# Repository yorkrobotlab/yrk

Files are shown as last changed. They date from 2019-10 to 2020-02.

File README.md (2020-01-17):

# York Robotics Kit

This is the repository of the York Robotics Kit, designed to allow features rich, ROS-ready robots to be quickly developed using the Raspberry Pi 3 and 4 computer devices.  

The documentation can be view on readthedocs at the following URL:

https://york-robotics-kit.readthedocs.io/en/latest/

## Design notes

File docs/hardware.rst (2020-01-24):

.. include global.rst
.. YRK User Guide: Connecting Hardware

*******************
Connecting Hardware
*******************

This section of the user guide explains how to connect hardware such as batteries, motors, servos and sensors to the **YRK** to make a complete electronics hardware design for a robot.  The simplified
pin-out diagram is shown below, a more detailed view is available in the ``Documents`` sections.

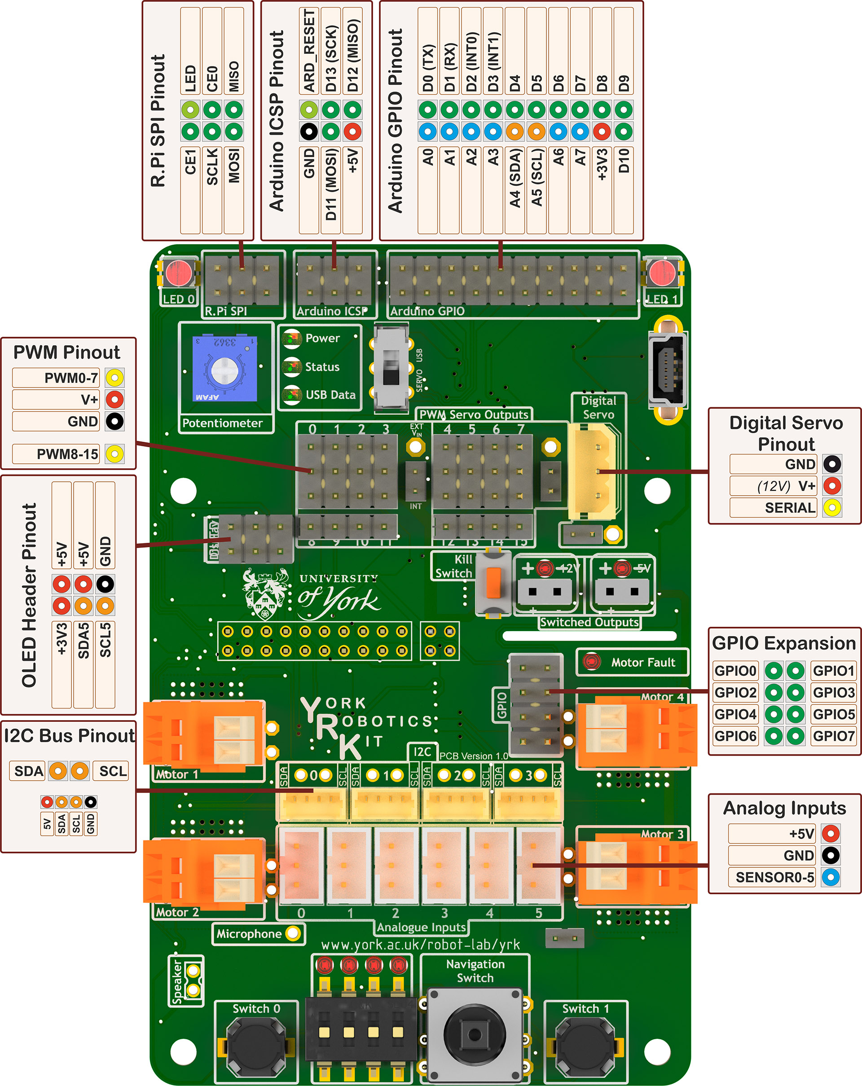
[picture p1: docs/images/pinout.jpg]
Pin-out and wiring diagram for York Robotics Kit


    Pin-out and wiring diagram for York Robotics Kit

Power Supply
------------

The YRK can be powered by any standard 12V power supply with a 2.1mm DC jack (centre positive) and 3A or greater current rating.  Using a tethered power supply such as this is strongly
recommended to be used as much as possible to preserve battery life if motion of the robot is not required.  Do not connect a power supply when the battery is connected and vice-versa *(shutdown
between changing power sources by pressing the power button)*.

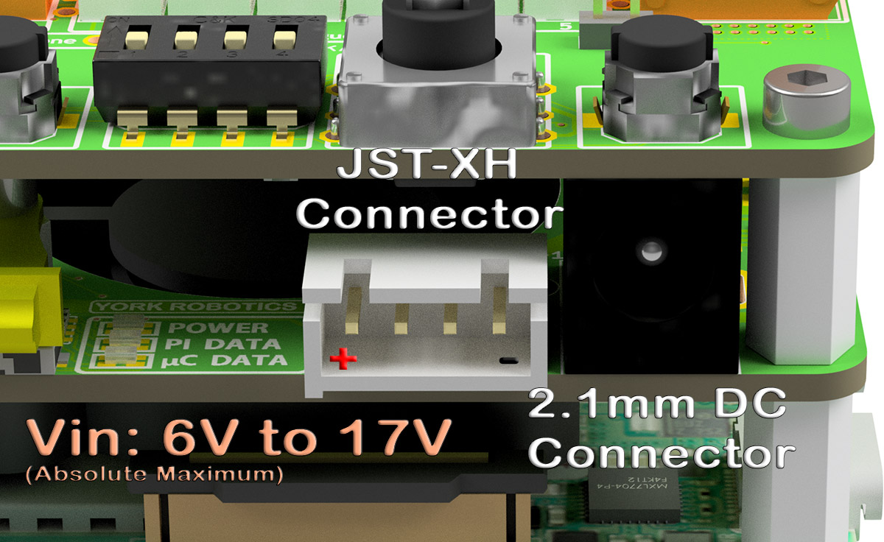
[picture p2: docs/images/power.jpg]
DC power jack and JST-XH power jack at front of YRK on YRL039 power supply board.


    Location of the 2.1mm DC jack and JST-XH battery connector

Battery
-------

The YRK is primarily inteded to be run using a 3-cell Lithium-Polymer battery pack, connected using the industry-standard **JST-XH** 4-pin 0.1" pitch connector
used as the balance charging connector.  These connectors and cables are typically rated for 2A current which is enough for normal use of the YRK [which has a **2.5A** input Polyfuse].  Where high
currents are needed, such as powering multi servo motors, the high current cable from the battery should be soldered *(via a self-made adapter)* to the appropriate power points on the **YRL040** PCB.

The **YRL039** power supply board has a low-voltage dropout and should work effectively from voltages as low as **5.5V** to a **17V** high, enabling 2-cell and 4-cell operation Li-Po (and a range
of other lead-acid, Ni-Mh, NiCad, LiFe and other rechargeable battery technologies, provided they can provide around 5A peak current at 5V).  Relevant changes to the ``yrk.settings`` file should
be made to reflect the battery used if not the default 3-cell configuration.

Only the outer-two connections of the **JST-XH** connector are used.  It is also possible to use the 2.1mm DC jack as the input source.  Always disconnect the battery after use and charge using a
suitable charger (in a fire-safe bag if using a Li-Po battery pack).  The power supply board is not presently optimised for ultra low-current and the residual current draw (from the ATMega microcontroller)
will discharge the battery even when beyond a damagingly low value.  General convention suggest a per-cell voltage of 3.0V is the absolute minimum a Li-Po battery should be allowed to discharge to *(ie 9V
for 11.1V 3-cell battery)* before permanent damage is likely to be done.  The Arduino code on the **YRL039** can be configured to automatically switch off power supplies below a critical low voltage but this
needs to be correctly configured for the battery technology used.  If the ``core.py`` software is *not* run the user must implement some method of periodically monitoring the battery voltage and provide
suitable user warnings when low levels are reached, otherwise batteries can rapidly deteriorate.

The YRK connected to a Raspberry Pi 4 will typically consume approximately 800mA on the 5V rails at idle, most the current powering the Raspberry Pi and a smaller amount of the **5V_AUX** rail (mostly
powering the fan and LEDs).  Motors and sensors will add significantly to this load.  This relatively high idle load means that battery capacity should be at least 1000mAH, and this capacity would
provide at best around 1 hours use *(and significantly less in high load cases)*.  The use of a lower-power Raspberry Pi, such as the model 3A, might be considered when long battery life on small batteries
is desired, at the expense of memory, processing capability and expandability.

DC Motors
---------

There are four serial H-Bridge motor drivers, based on the **DRV8830** `TI Motor Driver <http://www.ti.com/lit/ds/symlink/drv8830.pdf>`_.
The PCB design limits each motor driver to approximately **800mA** current, powered from the *5V_AUX* supply.  Having all four motors drawing this peak current
for sustained periods will exceed the rating of the power supply.  This current limit *(and voltage rating)* does restrict the motor driver to using small motors,
such as the widely-available 3mm shafted **micro-metal gear motors**.  Before using a different size of motor it is recommend to check *(such as by using a bench
PSU)* what the stall and no-load currents at **5V**.

The holes on the unpopulated PCB allow the motors to be connected to either **Wago** push-fit terminals or **(on PCB version 1.1)** 3.5mm pitch screw terminals.
With either connector, a remaining pair of holes will be accessible on the PCB should a direct soldered lead be required.  The motor driver can detect fault
conditions (undervoltage, overvoltage and overtemperature events) and when the ``yrk.core`` program is running these will be indicated by the red fault LED above
the top-right motor output.  If persistent fault conditions check the motor is working correctly and doesn't draw excessive current for the design; micro-metal-gear
motors are relatively delicate.  

Servos
------

The YRK can control both standard analogue servo motors (8 directly attachable, 8 further channels available via breakout), and digital servo motors via an
Arduino-based software interface.

Analogue Servos
^^^^^^^^^^^^^^^

Analogue servos are operated using a **PCA9685** `I2C LED driver IC <https://www.nxp.com/docs/en/data-sheet/PCA9685.pdf>`_.
Whilst primarily designed to allow I2C brightness control of up to 16 LEDs,  it can effectively work as a analogue servo controller.
Analogue servos typically operate with a **20mS** period width *(50Hz PWM frequency)*, and expect a pulse width in the **1ms - 2ms** range [with **1.5ms** being the middle point of the servo rotation].
The **PCA9685** lets us fix the PWM frequency for all outputs and effectively becomes an I2C servo controller.

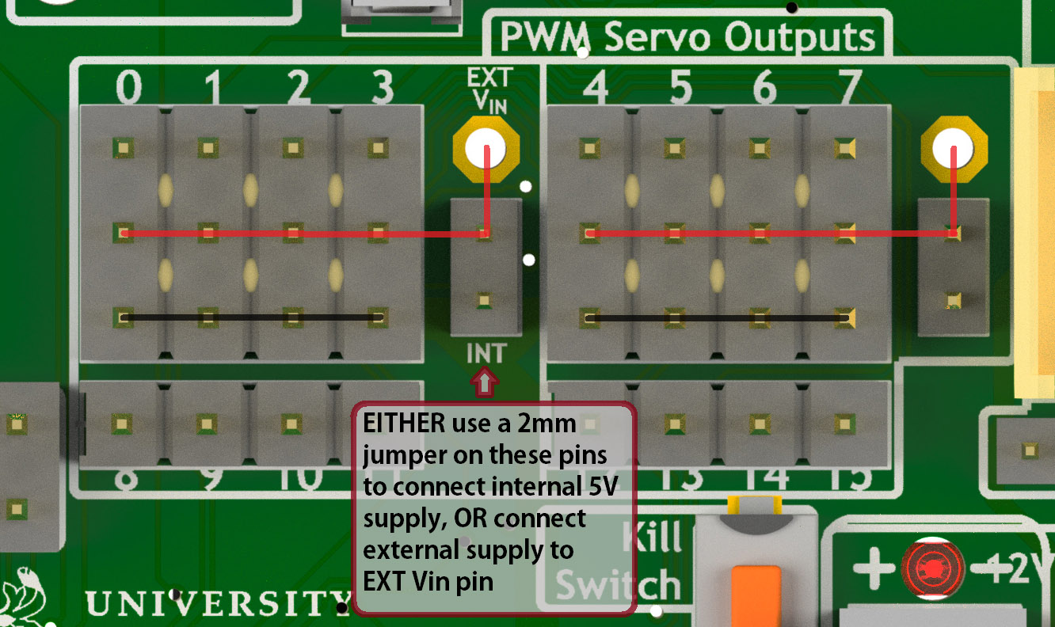
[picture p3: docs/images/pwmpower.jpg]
Power routing for 2 banks of PWM analogue servo outputs


    Power connections for the 2-banks of PWM analogue servo outputs

There are 16 available outputs on the YRL040 PCB, located in the middle-top of the PCB.
Eight of these are available as full 3-pin outputs, where DC power (**+** and **GND**) can be supplied to the servo.
Most analogue servos come hardwired with a three-pin 0.1” pitch socket attached at the wire tail.
Different colour schemes are used for the wiring, and it is important to be careful checking the orientation of the plug;
as a general rule the lightest colour will the control signal (top side of connector) and the darkest will be ground.

==========  =======   ======  ======  ===============
Pin Number  Signal    Futaba  JR      Hitec
==========  =======   ======  ======  ===============
3 [Top]     Control   White   Orange  Yellow or White
2           V+        Red     Red     Red or Brown
1 [Bottom]  Ground    Black   Brown   Black
==========  =======   ======  ======  ===============

These 8 complete connections are split into two banks of four.  Each of these banks can be supplied with DC either by the internal 5V supply **(by using a 2mm jumper)**, or to an external positive input, by soldering a suitable cable onto the hole on the board.  If the internal supply is used, the total current for each bank **must not excede 1A** (a pair of 0603 fuses are included on the board .  This is due to the overall current limitations on the board.  For this reason it is strongly recommended to only use very small, low-current servos, and to spread load across both banks, if using the internal supply.

Another 8 PWM outputs are available just below the primary 8, but these cannot be used directly with a 3-pin connector.  In situations where a large number of servos are required simultaneously, a small break-out board allowing direct power connection would be a sensible option.
The circuit is the same as used on the `Adafruit 16-channel PWM servo driver <https://learn.adafruit.com/16-channel-pwm-servo-driver>`_.

Code for the analogue servo control is in the :mod:`yrk.pwm` module.  Examples of the use of the PWM
driver to control servos can be found in :mod:`examples.console`.

Digital Servos
^^^^^^^^^^^^^^

The York Robotics Kit is designed to support digital servos from the **(Dynamix AX- and MX- series)** via code on the Arduino microcontroller.

To do: This section and code not completed yet!

Analogue Inputs
---------------

The YRK includes an I2C based, 8-channel, 8-bit analogue to digital converter IC.  Whilst this can be used for anything
requiring analogue inputs, it is primarily intended for use with analogue distance
sensors manufactured by Sharp, in particular the **2Y0A21** and **2Y0A41** models.  The reference voltage is set to **2.5V**,
meaning the returned value is approximately equal to the voltage mulitplied by 100.

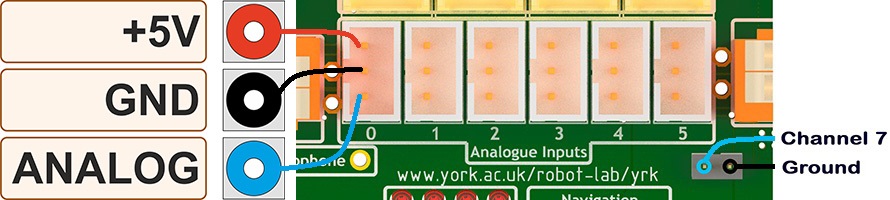
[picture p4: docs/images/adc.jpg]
Pin-out for channels 0-5 and channel 7 of the analog to digital converter


    Analogue input channels 0-5 *(JST PH sockets)* and channel 7

Cables
^^^^^^

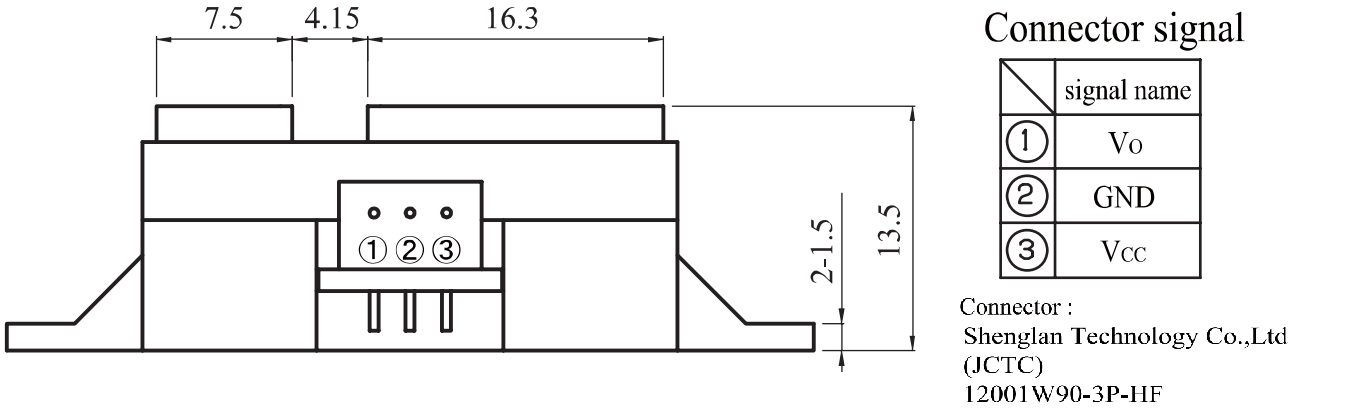
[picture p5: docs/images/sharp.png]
Wiring diagram of Sharp Distance Sensors


    Wiring diagram of Sharp Distance Sensors

The Sharp distance sensors use a 3-pin JST PH series connection **(note the newest models use a JCTC connector instead of
a JST)**.  6 matching JST-PH connections are available on the York Robotics Kit, each providing the analogue-input and 5V
power supply required by the sensor.  A suitable complete pre-made harness has not been sourced, but it is possible to buy
pre-crimped leads from JST which make creating harnesses quick and simple *(if expensive)*.

===============   ============  ===================  ======================
JST Part Number   Farnell Part  Description          Unit Price *[per 100]*
===============   ============  ===================  ======================
01SPHSPH-26L150   2065431       150mm PH-PH Lead     0.416
01SPHSPH-26L300   2065432       300mm PH-PH Lead     0.439
PHR-3             3616198       3-pin PH Receptacle  0.032
===============   ============  ===================  ======================

To assemble the harness, place one receptacle face-up and the other face-down then connect top-to-top, middle-to-middle and bottom-to-bottom,
as seen in the photograph below.

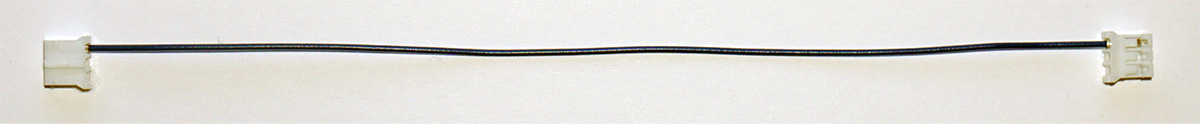
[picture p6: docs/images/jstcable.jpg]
Assembly of a JST PH cable for use with Sharp Distance Sensors


    Assembly of first wire in JST PH cable for use with Sharp Distance Sensors

Datasheets
^^^^^^^^^^

`Sharp 2Y0A21 [10-80cm] <https://global.sharp/products/device/lineup/data/pdf/datasheet/gp2y0a21yk_e.pdf>`_

`Sharp 2Y0A41 [4-40cm] <https://global.sharp/products/device/lineup/data/pdf/datasheet/gp2y0a41sk_e.pdf>`_

Potentiometer
^^^^^^^^^^^^^

Channel 6 of the ADC is connected to a potentiometer *(variable resistor)* at the top-left of the PCB.  As the pot'
is rotated clock-wise from left to right the ADC output value will **decrease** from 255 to 0.

Other ADC Inputs
^^^^^^^^^^^^^^^^

Channel 7 of the ADC is routed to the left pin of a 2mm pitch pin-header below the channel 5 connector.  Any of
channel 0-5 and 7 can be used as a general purpose ADC input (8-bit, with a 2.5V reference voltage) by using the
raw reading value.  There is also the potential to use any of the 8 available analogue inputs on the ATMega microcontroller which offers 10-bit
resolution *(see section on Arduino below)*.

I2C Devices
-----------

The I2C interface is widely used for many robotics sensors and accessories.  The YRK uses a **PCA9548** I2C
switch, which splits the master I2C bus into 8 individual busses, allowing the use of repeated I2C addresses
across multiple ports.  This allows, for example, the use of multiple I2C distance sensors which share the
same I2C address, by connecting them to different busses.  Most I2C devices (capable of operating in **400KHz**
*fast mode*) can be attached provided they do not use the address **0x70** which is used by the switch.

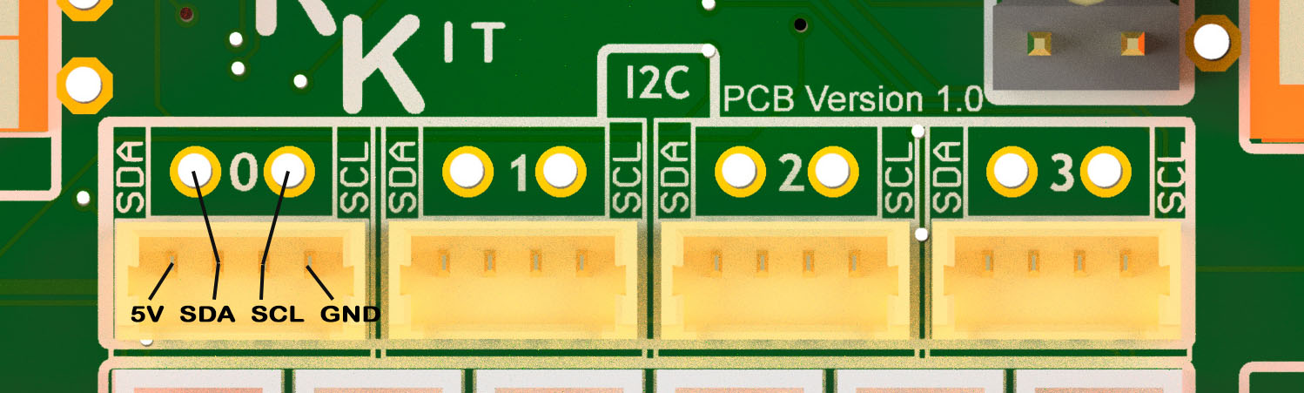
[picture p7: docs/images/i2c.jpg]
Closeup of I2C (channel 0 - 3) Picoblade and 0.1" connectors


    Closeup of I2C (channel 0 - 3) Picoblade and 0.1" connectors

The I2C switch has a kernel-level driver, meaning that the individual switched busses appear to the user as
different I2C root devices (each has its own file handle at ``/dev/`i2c-XX``).  The actual address of the bus
is different when used on the Raspberry Pi 4 hardware and earlier versions, as the Raspberry Pi 4 hardware
can support more native I2C busses (not used in the **YRK**).  On the Raspberry Pi 4, the switched busses map
to file descriptors ``/dev/i2c-6`` to ``/dev/i2c-13`` from channel 0 to 7, and to descriptors ``/dev/i2c-3`` to ``/dev/i2c-10``
on earlier version of the Pi.

The first four channels are unused and are intended for user additions.  These SDA and SCL signals for these channels are each routed to
unpopulated 0.1" pitch holes on the YRK PCB, and also to 4-pin Molex Picoblade headers.  The Picoblade headers (1.25mm pitch) include a
5V and GND signal.  These are directly compatible with sensor boards developed at York such as the **YRL013** multi-sensor board and the
**YRL019** thermal-imaging sensor board.  Note that all i2c channels except channel 4 are pulled-up to 3.3V; channel 4 is
utilised by the PWM driver and the Arduino *(see below)* and is pulled-up to 5V.

Arduino
-------

The YRK includes a **ATMega328P** microcontroller, running at **5V** and connected to both an
FTDI serial to USB interface and to the I2C switch (on switch port 5, which is ``/dev/i2c_11`` on Pi 4).
The microcontroller is effectively a clone of an Arduino Nano board (albeit with a different pin layout).

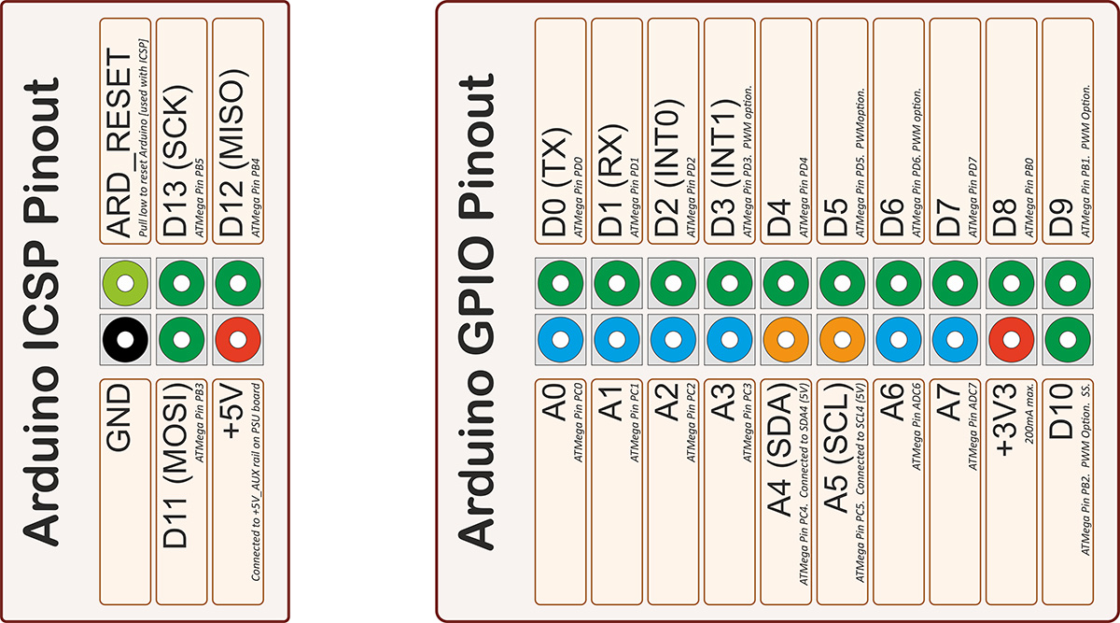
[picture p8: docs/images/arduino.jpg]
Pinout for ATMega microcontroller expansion


    Pin-out for the ATMega microcontroller *(Arduino nano clone)*

Programming Bootloader
^^^^^^^^^^^^^^^^^^^^^^

Before normal use, the ATMega328P must have bootloader code uploaded to it which allows it to be programmed
using the serial to USB interface.  This can be done using various AVR programmers, but can also be done
using a separate Arduino board and the `Arduino as ISP <https://www.arduino.cc/en/tutorial/arduinoISP#toc2>`_
program.  The best settings in the Arduino IDE are to use ``Board: Arduino Pro or Pro Mini`` and ``Processor:  ATMega328P (5V, 16MHz)``.

Uploading Code
^^^^^^^^^^^^^^

Once the bootloader has been uploaded, the Arduino can be programmed via the mini-USB port at the top-left of the board.
Note that the 5V power on the mini-USB is not connected to the YRK *(this means the YRK board needs to be powered on if programming
over USB).  It is possible to program the Arduino from the Raspberry Pi, if a USB cable is connected from the mini-USB to the USBs on the
Pi.  This can be done either using Arduino IDE, or from the command line *(avoiding the need for X-windows)*.  The command line upload
would look similar to this statement::

  arduino --upload --port /dev/ttyUSB0 --board arduino:avr:pro:cpu=16MHzatmega328 --verbose-upload my_code.ino

It is important to note that to use the mini-USB interface the slide-switch must be in its upper position.  The switch
directs the **TX** and **RX** serial output pins from the ATMega microcontroller to either the **FTDI** serial to USB interface *(and mini-USB port)*,
if it is in its upper position, and combines the lines via a tri-state buffer for use with the digital servo port in its lower position.

Switched Outputs
----------------

The board contains a pair of **FET** driven switched outputs which can be used when it is necessary to turn
on simple switched loads.  Typical uses might be powering buzzers and sirens, LED light fittings and lamps,
beacons, solenoids and relays.  One output is connected to the **5V_AUX** supply, the other is marked as **12V** and is
connected to the battery or DC input.  Both switched outputs are protected by a 1A 0603 quick-blow fuse.  The outputs are
connected to 0.1" sockets *(preferred over header as harder to short-circuit)*.

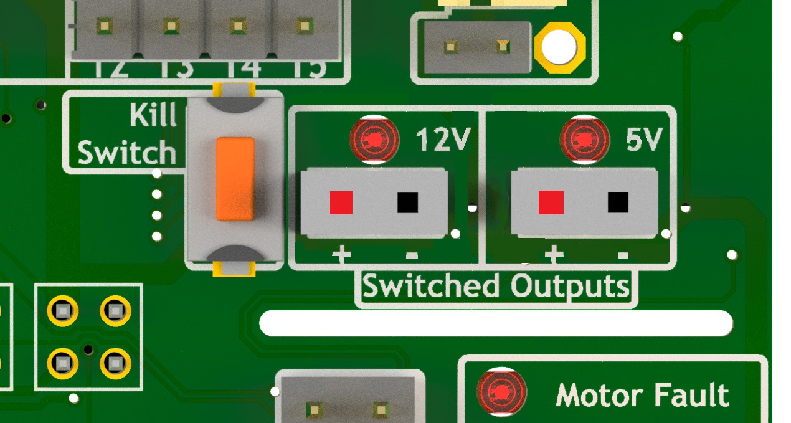
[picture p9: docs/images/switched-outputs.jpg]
Switched output connectors


    Close-up view of 12V and 5V switched output connectors.

It is important to note that the switched outputs use low-side switching, meaning that the **+** output is connected directly
to the *(5V or battery)* supply rail but the **-** is **not** connected to ground; never use the switched outputs on loads
that require the grounds to be coupled together.  It is recommended to limit the current on the switched outputs to below 500mA
if possible.  If a higher current (or circuit with coupled ground) is needed, consider using the switched load to drive a relay
or solid-state equivalent.   Note that the actual potential difference will be a little lower than the indicated amount due to
the voltage drop across the **FET**.  Consider using a flyback diode across inductive loads (such as relays and solenoids).

Raspberry Pi Interfaces
-----------------------

One consequence of the number of hardware features on the board is that very few Raspberry Pi GPIO pins are available for use.  The
5 pins that are available (pins 19, 21, 23, 24 and 26) are the pins that can be used as the SPI0 interface on the Raspberry Pi,
allowing SPI peripherals and expansion to be added to the YRK.  These pins can also be used a general purpose IO pins if the SPI
interface is not required.

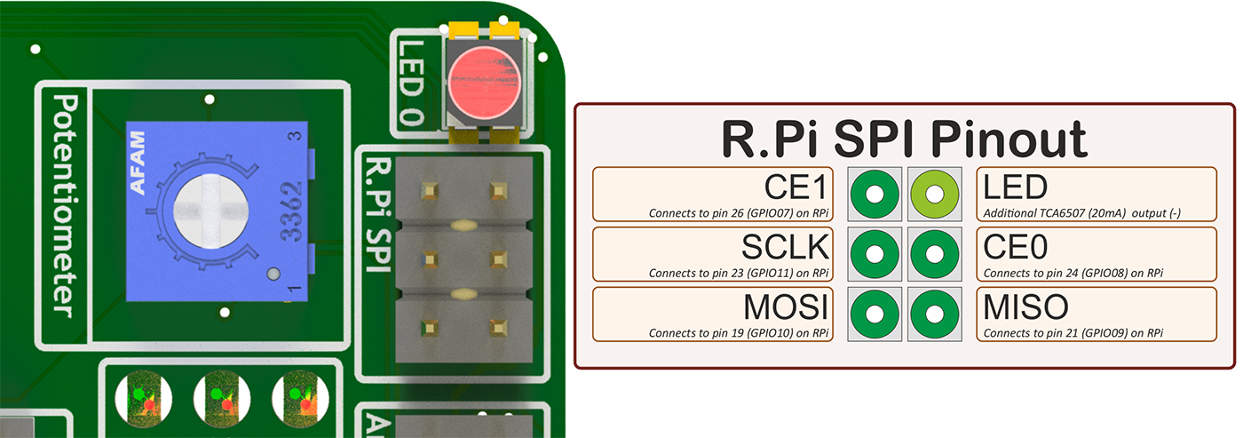
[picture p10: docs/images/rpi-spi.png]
View of RPi - SPi connector


    Close-up view of Raspberry Pi SPI interface at top-left of board (rotated 90 degrees)

Additional GPIO
---------------

A bank of 8 user-GPIO pins connected to the bank 0 of the *(U13)* **PCA9555PW** GPIO expansion IC is available for use.  The API for the pins is
not yet written.

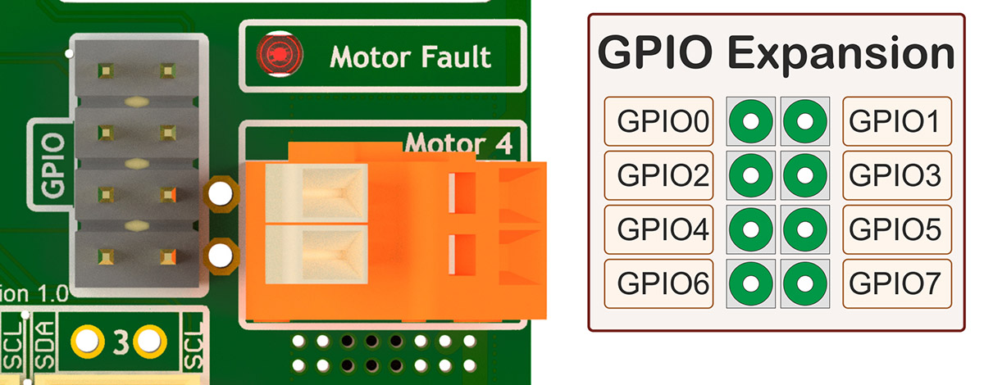
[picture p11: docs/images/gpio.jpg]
View of user GPIO


    Close-up view of 8 user GPIO expansion pins

There are several other expansion pins on the board that can be used as general purpose digital IO pins, for connecting extra hardware
such as switches, LEDs, transistor switches and others.  The **TCA6507** LED driver that drives the RGB LEDs has one additional output that
is configured to give a 20mA drive current to an external LED *(or multiple LEDs in series or parallel)*.  The cathode pin of the LED(s) should
be attached to the LED pin of the ``R.Pi SPI`` header at the top-left of the PCB; the anode can be connected to either a 3.3V or 5V pin as needed
*(blue and white LEDs may require 5V due to their greater forward voltage)*.  The PWM (analogue servo) outputs can also be used to drive LEDs
or other outputs if appropriate *(the PCA9685 driver is actually marketed as a LED driver)*.

Display
-------

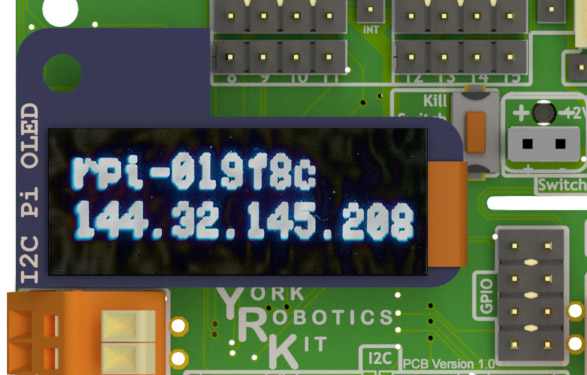
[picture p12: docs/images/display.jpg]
OLED I2C Module attached to the YRK


    Close-up view of Adafruit I2C OLED display module on YRK

The board has been designed such that an **Adafruit PiOLED** 128x32 pixel display module can be directly connected to the main board.
The software library written by Adafruit has been adapted so that it performs more reliably on the switched I2C bus *(note that I2C
is a relatively slow bus and even small displays take quite a lot of data to drive, so infrequent updates are recommended)*.

Obviously it may be desirable to relocate the display elsewhere on a robot chassis if the YRK and Pi are enclosed within; this simply
requires the use of either 4 jumper leads or ideally a **3x2x0.1"** IDC patch cable from the header on the **YRK** to the receptacle on
the display PCB.

It should be possible to use different I2C (and also SPI) displays but some alteration of code may be necessary to handle the i2c switch.
It will not be possible to use any display modules which rely on a large number of GPIO pins on the Raspberry Pi as these are not available
once the YRK is added.  If a larger display is required, consider using the official Raspberry Pi touch display *(7" diagonal)* or a HDMI
based solution.

Loudspeaker
-----------

The YRK includes a monoaural amplifier attached to one of the PWM outputs of the Raspberry Pi **(GPIO12)**.  When correctly configured, the
Raspberry Pi (using the **ALSA** audio system) can be set to play audio using its internal PWM.  The **YRL040** PCB includes a Texas Instruments
`TPA2005 <http://www.ti.com/lit/ds/symlink/tpa2005d1.pdf>`_ class-D audio amplifier IC, which is capable of producing up to 1.4W when using an 8-ohm
speaker.  It may be possible to use lower impedance speakers (down to 4-ohm) but note the amplifier is using the **5V_AUX** and would be operating
out-of-specification at 4-ohms.  Audio generated from PWM outputs is generally very noisy and low in fidelity but is adequate to generate simple
sounds and speech synthesis.

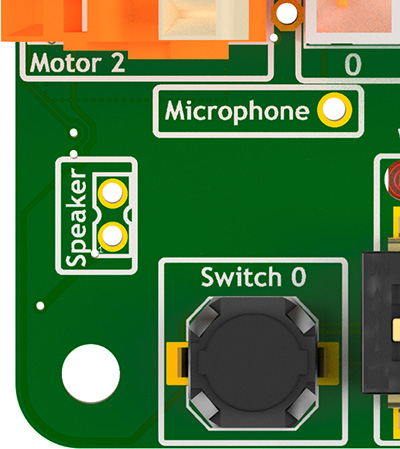
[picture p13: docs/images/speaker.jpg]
Location of speaker connection at bottom left of board


    Location of the speaker connection at bottom left of YRL040 PCB

The speaker output is routed to two pin holes near the bottom-left corner of the **YRL040 PCB** *(being mono the phase of the speaker
doesn't matter)*.  A 2-pin, 2mm pitch header can be soldered in place here to make attaching a removable speaker easier; it hasn't been done by default as
the case has space for a 17mm x 11mm speaker to be connected which would be hard-wired to the underside of the *YRL040* PCB.

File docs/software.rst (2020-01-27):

.. include global.rst
.. YRK User Guide: Software Setup

**************
Software Setup
**************

This user guide covers the software setup of the **YRK**.  It assumes that the micro-SD
card in the Raspberry Pi is using the pre-built **Raspbian** installation (*YRK Raspbian*)
created for the York Robotics Kit, that includes the **ROS Melodic**,  **OpenCV 4** and the
Python 3 virtual environment with all the prerequisite packages installed, along with a clone
of the **Git** repository available at::

   https://github.com/yorkrobotlab/yrk

The detailed software setup procedure followed to create the image is available in a different
document.  In the default image, the username is **pi** and the password is **robotlab**.

YRK Raspbian
------------

This document is written for **YRK Raspbian Build 23/01/2020**.  This build of Raspbian contains
the following software installations:

* Raspbian Version: Buster *(Raspbian GNU/Linux 10)*.  Output of ``lsb_release -a``

* Kernel: Linux 4.19.75-v71+ #1270 Sep 24 2019 armv71.  Output of ``uname -a``

* OpenCV: 4.1.1  Output of ``cv2.__version__`` in Python

* ROS: Melodic  Output of ``rosversion -d``

* Arduino:  1.8.10  Output of ``arduino --version``

The **yrk** PYthon virtual environment is preinstalled with a large number of required packages.
The list of packages can be found in the ``requirements.txt`` file in the ``/home/pi/yrk`` folder,
or by using the ``pip freeze`` command.

First Run
---------

The image is preconfigured to work with the ``robotlab`` wi-fi network at York; if needed, make
changes to ``/etc/network/interfaces`` before booting *(by editing the SD card in a different
Linux system)*, or connect the Pi to a display and configure networking.  Obviously in normal use
the YRK is intended to be connected to remotely using SSH or VNC etc.

On first boot of a clean install of **YRK Raspbian Build 23/01/2020** it is recommended
to update the system.  Make sure all DIP switches are in their **OFF** **(down)** position.
From the ``/home/pi`` folder execute the following script::

  . update.sh

This will update Raspbian using ``apt update`` and ``apt upgrade``,  perform a Raspberry Pi
firmware upgrade using ``rpi-eeprom-update``, run ``fixhostname.sh`` to check the hostname
has been update to the form **rpi-XXXX** *(where XXXX is last 4 digits of MAC address)*.  It
will then update to the latest codebase for **git** using ``git pull``, and clean and rebuild
the HTML documentation using ``make clean`` and ``make html`` from the docs folder.

Once the networking is setup and the system updated, the should be able to use the YRK in its
normal operating mode.  The current release defaults to booting the X-server *(even without display
attached) and auto-login; it is easy and recommended to change to command-line only using the
``raspi-config`` tool if graphical user interface isn't needed.  Both SSH and VNC *(remote-desktop)*
are enabled by default.

The documentation *(this file!)* is built in **HTML** format in the ``/home/pi/yrk/docs/_build/html/``
path, using the **Sphinx** document generation system.

Boot Procedure
--------------

The image contains entries in the ``.bashrc`` file that set the Python virtual environment to
**yrk**.  It then looks to see if the device ``/dev/i2c_11`` exists.  If the **YRK** is connected
and working correctly the i2c multiplexer device tree should be running, enabling 8 extra i2c
busses (named ``/dev/i2c_6`` to ``/dev/i2c_13`` on the **Pi 4** and ``/dev/i2c_3`` to ``/dev/i2c_11`` on the **Pi 3**).

If the device is found, the shell scripts ``/yrk/bootscript.sh`` will be launched.  It is important
to note that both scripts are called every time a new session is started (such as every new **ssh** connection).
A *core program* is run on the first call of ``bootscript.sh`` after each reboot, described in detail in the
next section.  The *core program* writes files to an area of temporary storage at `/mnt/ramdisk/`.  The
**DIP** switches at the bottom of the **YRK** determine the operation mode at boot-up, described in more detail in the next section.

The default working directory is::

   /home/pi/yrk

To kill Python processes, erase the ramdisk and restart ``bootscript.sh`` quickly use the script::

   . rerun

Core Program
------------

The core program :mod:`yrk.core` performs certain core functions that aim to improve usability
and reliability of robot controllers.  This include monitoring battery, temperature and fault
conditions, and monitoring the user switches.  It also provides the functionality to control
the *ROS* service, a web service and a demo program.  This functionality is provided through the
4-way **DIP** switch at the bottom of the kit.

* Switch 0 (*marked as 1 on the switch itself*) determines if the core program should be run on boot.
  If disabled, ``core.py`` will not be run.  This is often useful for testing but user needs to
  remember to keep check on battery and temperature.
* Switch 1 enables the ROS service using ROS launch.  If the switch is disabled after ROS has been
  launched the process will be killed, allowing a relaunch.
* Switch 2 enables the web service.  This enables a **Flask** webserver running a **Dash** site with **DAQ**
  components and this manual.  By default at ``localhost:8080``.
* Switch 3 enables the demo program.  [To do...]

Basic Programming Examples
--------------------------

Before using the ROS infrastructure to program the **YRK** it is worth considering some very simple
low-level example programs.  We shall look at how to write very basic programs that access low-level
features; it is recommended that the core program, normal Python services and ROS services are **not**
running when programming like this.  Remember that if the core program isn't running, automatic battery,
temperature and fault monitoring will not be running.

The code examples in the section are all Python programs that should be run in the **yrk** virtual
environment (this should be enabled by default in the image and is indicated by a ``(yrk)`` before the filepath
in the terminal console).  The examples below can be written in a text-editor, or can be entered directly into
the *Thonny* Python IDE using the VNC connection.  For proper code development working on the Pi over VNC isn't
recommended but it can be useful for quick tests such as this.

Motors Example
^^^^^^^^^^^^^^

The first example program below sets the motor connected to driver 0 *(labelled as Motor 1 on the PCB)* to 50 percent forward
duty-cycle.  We import the :mod:`yrk.motors` module from the **yrk** library as ``motors`` and call the :meth:`yrk.motors.set_motor_speed` method::

  import yrk.motors as motors
  motors.set_motor_speed(0,0.5)

As the **YRK** is designed to be flexible in robot topology, the :mod:`yrk.motors` is limited to functions that affect one motor at a time,
with the exception of :meth:`yrk.motors.stop_all_motors` which sets all 4 outputs to their stopped, high-impedance state.  The following code
shows an example of how simple drive functions for a two-wheels, skid-steered robot, with motors connected to driver 0 and 3 *(labelled as Motor 1
and Motor 4 on the PCB)*.  By adjusting the speeds and the sleep times, it should be possible to make the robot move in a square path::

  import yrk.motors as motors
  import time

  def forwards(speed):
        motors.set_motor_speed(0,speed)
        motors.set_motor_speed(3,speed)

  def turn(speed):
        motors.set_motor_speed(0,speed)
        motors.set_motor_speed(3,-speed)

  def brake_motors():
        motors.brake_motor(0)
        motors.brake_motor(3)

  for i in range(4):
        forwards(0.5)
        time.sleep(0.5)
        brake_motors()
        time.sleep(0.1)
        turn(0.5)
        time.sleep(0.5)
        brake_motors()
        time.sleep(0.1)

   motors.stop_all_motors()

ADC Example
^^^^^^^^^^^

The module :mod:`yrk.adc` contains the methods for reading the analog:digital converter.  The module :mod:`yrk.led` contains
methods for controlling the RGB LEDs.  We can combine all three to use the on-board potentiometer *(attached to ADC channel 6)*
to set the motor speed for driver 0 and set the LED brightness proportional to speed::

  import yrk.adc as adc, yrk.motors as motors, yrk.led as led, time
  while(True):
        #Read raw value of pot. 255 is fully_left, 0 is fully_right
        pot_value = adc.read_adc(6)
        #Set motor 0 speed to be fully backwards [-1.0] at pot=fully_left and
        #fully forwards [1.0] at pot=fully_right
        motors.set_motor_speed(0, 1.0 - (0.007843 * pot_value))
        #Set led brightness to be proportional to speed (range is 0-15)
        led.set_brightness((abs(128-pot_value) + 6) >> 3)
        #Make the LEDs white
        led.set_colour_solid(7)
        #Add a short wait to keep system responsive
        time.sleep(0.01)

.. warning::
   This code will spin motor 0 and set the LEDs to a high brightness unless the potentiometer
   is very close to its central position.

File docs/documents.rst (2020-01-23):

.. include global.rst
.. YRK User Guide: Additional Documents

********************
Additional Documents
********************

This section contains links to other useful documents such as electronic design files, 3D models files
and datasheets for many of the core components use on (or designed for use with) the York Robotics Kit.

.. _schematics:

Schematic Diagrams
------------------

The Eagle design files and bill-of-material files for the **YRL039** and **YRL040** PCB
The schematic diagrams and Eagle design files are available in the ``pcb_documents`` subfolder of the YRK
repository.

========================================================================================   ============================================================================
File                                                                                       Description
========================================================================================   ============================================================================
`yrl039-schematic.pdf </home/pi/yrk/pcb_documents/pdf/yrl039-schematic.pdf>`_              Schematic diagram for the **YRL039** Power Supply Board
`yrl039-top.pdf </home/pi/yrk/pcb_documents/pdf/yrl039-top.pdf>`_                          Top silkscreen view of the **YRL039** Power Supply Board
`yrl039-toptraces.pdf </home/pi/yrk/pcb_documents/pdf/yrl039-toptraces.pdf>`_              Top copper layer view of the **YRL039** Power Supply Board
`yrl039-bottomtraces.pdf </home/pi/yrk/pcb_documents/pdf/yrl039-bottomtraces.pdf>`_        Bottom copper layer view of the **YRL039** Power Supply Board
`yrl040-schematic.pdf </home/pi/yrk/pcb_documents/pdf/yrl040-schematic.pdf>`_              Schematic diagram for the **YRL040** York Robotics Board
`yrl040-top.pdf </home/pi/yrk/pcb_documents/pdf/yrl040-top.pdf>`_                          Top silkscreen view of the **YRL040** York Robotics Board
`yrl040-bottom.pdf </home/pi/yrk/pcb_documents/pdf/yrl040-bottom.pdf>`_                    Bottom silkscreen view of the **YRL040** York Robotics Board
`yrl040-toptraces.pdf </home/pi/yrk/pcb_documents/pdf/yrl040-toptraces.pdf>`_              Top copper layer view of the **YRL040** York Robotics Board
`yrl040-bottomtraces.pdf </home/pi/yrk/pcb_documents/pdf/yrl040-bottomtraces.pdf>`_        Bottom copper layer view of the **YRL040** York Robotics Board
`yrl040-alltraces.pdf </home/pi/yrk/pcb_documents/pdf/yrl040-alltraces.pdf>`_              Bottom view of the **YRL040** York Robotics Board showing both copper layers
========================================================================================   ============================================================================

Datasheets
----------

This table contains internet URLs to most of the core intergrated circuits and modules in use on the **YRL039** and **YRL040** PCBs.

================  ==================  ====================================================================================
Component         Part Name           Datasheet URL
================  ==================  ====================================================================================
Arduino IC        ATMega328P          `<https://www.microchip.com/wwwproducts/en/ATmega328p>`_
I2C Switch IC     PCA9548             `<http://www.ti.com/lit/ds/symlink/pca9548a.pdf>`_
Serial:USB IC     FTDI FT232RL        `<https://www.ftdichip.com/Support/Documents/DataSheets/ICs/DS_FT232R.pdf>`_
Power Supply IC   TPS82130            `<http://www.ti.com/lit/ds/symlink/tps82130.pdf>`_
GPIO Expander IC  PCA9555             `<https://www.nxp.com/docs/en/data-sheet/PCA9555.pdf>`_
LED Driver IC     TCA6507             `<https://www.ti.com/lit/ds/symlink/tca6507.pdf>`_
Motor Driver IC   DRV8830             `<https://www.ti.com/lit/ds/symlink/drv8830.pdf>`_
PWM (Servo) IC    PCA9685             `<https://www.nxp.com/docs/en/data-sheet/PCA9685.pdf>`_
Audio Amp IC      TPA2005             `<http://www.ti.com/lit/ds/symlink/tpa2005d1.pdf>`_
Distance Sensor   GP2Y0A21            `<https://global.sharp/products/device/lineup/data/pdf/datasheet/gp2y0a21yk_e.pdf>`_
Distance Sensor   GP2Y0A41            `<https://global.sharp/products/device/lineup/data/pdf/datasheet/gp2y0a41sk_e.pdf>`_
================  ==================  ====================================================================================

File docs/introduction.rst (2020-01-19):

.. include global.rst
.. YRK User Guide: Introduction

************
Introduction
************

The **York Robotics Kit** is a platform design to allow the Raspberry Pi family of microcomputers
to control a wide variety of robotics hardware with the minimum extra electronics assembly.
It comprises a pair of PCBs which attach above a Raspberry Pi SBC *(single-board computer)*.
This document describes the initial version of the York Robotics Kit, comprising the **YRL039** Power
Supply Board and the YRL040 YRK Board, which are primarily designed to be used with the
Raspberry Pi 4 B and Raspberry Pi 3 B(+) series of computers.

This is still very much a prototype and development design and should be regarded as such!

Construction
------------

.. sidebar:: YRL040 PCB Variants

   **1.0** *[Sep 2019]* Original version as seen in pictures, models and diagrams

   **1.1** *[Dec 2019]* Navigation switch changed to surface-mount model, support for 3.5mm screw terminals for motors added.

This document assumes PCBs have been manufactured and all components assembled **(see separate documentation for PCB construction)**.
The PCBs have been designed using Autodesk Eagle software and are both 2-layer construction, designed to conform to Eurocircuits
Class 6 design guidelines.
Information about the Eagle CAD source files, schematic diagrams and layout documents can be found in the :ref:`schematics` section.
Both PCBs are two-layer boards and designed to be both relatively cheap to manufacture and relatively easy to assemble.

========  ================
PCB Name  Description
========  ================
YRL039    Power Supply PCB
YRL040    Main YRK PCB
========  ================

YRL039 Power Supply
-------------------

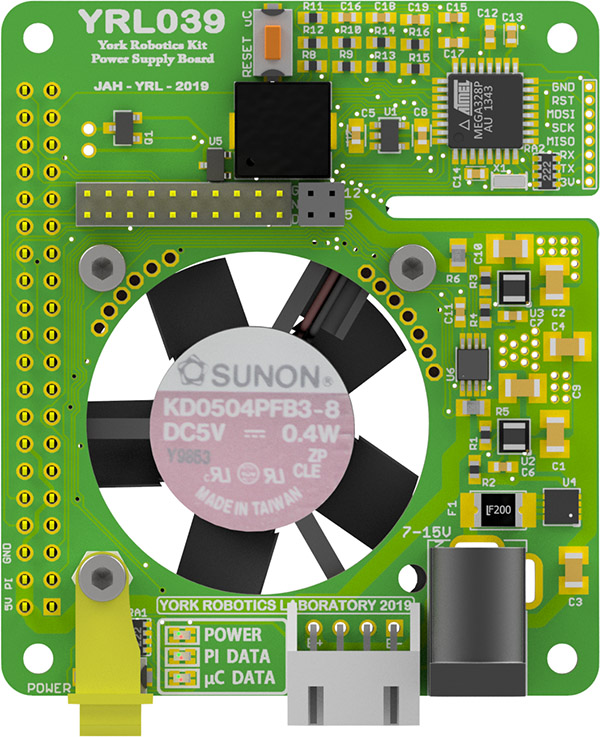
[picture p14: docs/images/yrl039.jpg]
3D rendering of the top of the YRL039 power supply


    YRL039 Power Supply

The YRL039 Power Supply Board as designed to serve six main functions:

* Take a battery or DC input and convert into stable, separate 5V supplies.  Each of the 2 5V supplies is rated to provide at least **2.5A** current.  One supplies the Raspberry Pi *(including USB peripherals)*, the other provides the **5V_AUX** rail for most other components.

* Provide an interface between Pi GPIO pins and respective pins on YRL040 PCB.  It was desired to rotate and reduce in size the 40-pin GPIO header on the Pi to allow more space for edge-mount connectors on either side of the YRL040 PCB **(for motors, sensors and servos etc)**.

* Provide hardware monitoring of temperature, input voltage, output voltages and output currents.

* Provide a software on-off power button with forced shutdown option

* Provide an 35mm fan based active cooling for the Pi microcontroller, the power supplies and the YRL040 mounted above.

* Generate simple audio tones using a Piezo buzzer

All the components except for the fan are mounted to the top-side of the PCB.  The **TPS82130** `TI 3A Step-Down Converter Module <http://www.ti.com/lit/ds/symlink/tps82130.pdf>`_ is core components of each of the two 5V power supplies.

Programming the YRL039
^^^^^^^^^^^^^^^^^^^^^^

The YRL039 uses at ATMega328P microcontroller to control the soft-power switch, make audio tones and report voltage, current and temperature readings using the I2C
bus.  The standard code is found in the ``atmega_code/yrl039_arduino`` subfolder of the GIT repository; if special functionality is required, such as lowering the
battery-low cutoff voltage or reducing the temperature at which the fan operates, it may be necessary to reprogram the microcontroller.  This is easiest to do with
the **YRL030** *FTDI Interface and Programming Board* that contains the 8-pin, 1.25mm pitch connector used for programming and serial data; the **YRL030** can be used
for both flashing the bootloader to the microcontroller using the **ICSP** interface and also uploading code and debugging data using a USB serial interface.

YRL040 Main PCB
---------------

The main YRL040 PCB has been designed such that the vast majority of electronic components are surface mounted on the underside of the board.

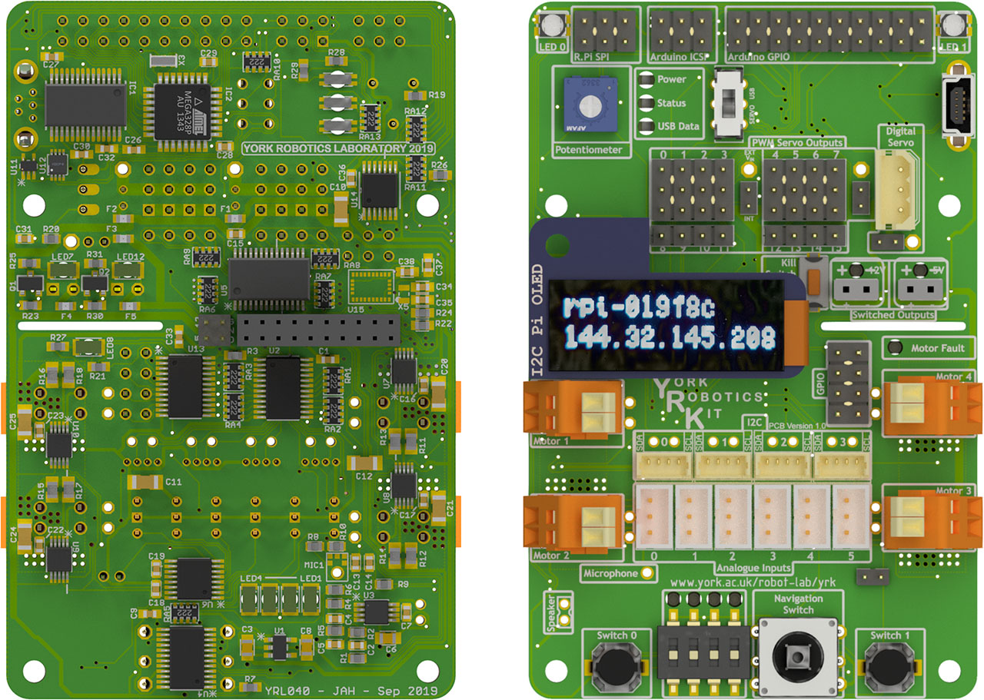
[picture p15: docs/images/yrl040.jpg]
Bottom and top 3D renderings of the top of the YRL040 PCB


    YRL040 Main PCB *(Bottom and Top Views)*

The board contains the following interfaces:

* 8-way I2C switch providing 4 user busses at 3.3V, a 5V bus used by on board PWM driver and Arduino, a bus
  design for use with an OLED display module, a bus for communication with the YRL039 PSU and a bus for all
  other internal connections.

* 4 I2C H-Bridge Motor Drivers based on the TI **DRV8830** IC.

* 16-channel PWM Driver suitable for use with analogue servo motors

* 16-channel GPIO expander providing 5-way navigation switch, 4-way DIP switch, 2 push-button switches and LEDs

* Addition 16-channel GPIO expander providing motor driver fault monitoring, a 5V and a 12V switched output,
  a kill-switch and 8 user GPIO pins

* 8-channel, 8-bit ADC with 6 ports optimised for use with Sharp analogue distance sensors, a channel connected
  to a potentiometer and a spare channel.

* A mono audio amplifier connected to a PWM audio channel on the Raspberry Pi

* An I2S mono microphone module

* An Arduino compatible ATMega328P microcontroller for use with wheel encoding, digital servo motors and other
  tasks.

Assembly
--------

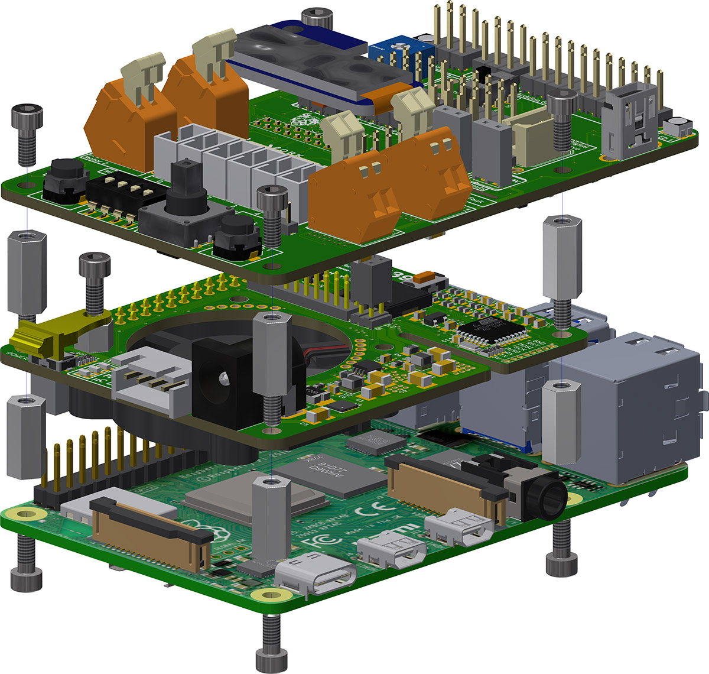
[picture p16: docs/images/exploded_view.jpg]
Exploded view of York Robotics Kit assembly


    Exploded view of YRK showing 11mm standoffs and M2.5 screws

The YRL039 attaches above the Raspberry Pi PCB using the 4 x 11mm length, M2.5 diameter standoffs.  Another layer of 4 x 11mm standoffs is used to attach the *YRL040*
PCB above the **YRL039** power supply PCB.  It is recommended that *M:F* **(male one end, female other)** standoffs are used in the upper layer, with the male threads pointing downwards through the *YRL040* PCB, then M:M standoffs **(sometimes called spacers)** below on the bottom layer.

The assembly can be mounted inside a further case, described below, or can be mounted directly onto a chassis or further standoffs.  Consideration of the airflow path should be taken, particularly when fully enclosed inside a robot.  The Raspberry Pi alone can generate a significant amount of heat and rapidly reaches a point at which it will throttle clock speed if it is not adequately cooled.

Case
----

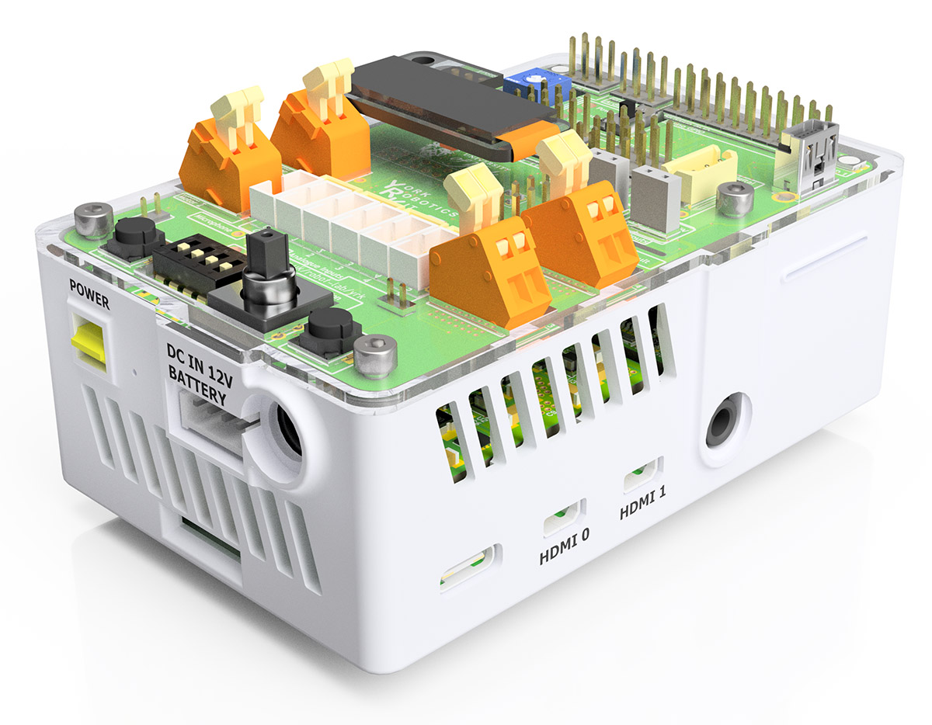
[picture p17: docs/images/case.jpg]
YRK mounted within case


    York Robotics Kit mounted in Polyjet case

A case designed *specifically* for the **Raspberry Pi 4B** series of computer, the **YRL039** and the **YRL040** PCBs has been designed.  This particular design is intended to be printed on a Polyjet class of 3D printer, with very fine tolerancs and gaps.  A more general design for FDM could easily be implemented, but is not essential.  If designed a new housing [or placing assembly within a robot chassis design etc], consider airflow route carefully.  Pi 4 devices will generate substantial heat and the fan needs some route to direct air across the Pi 4 CPU, but also ideally the power supply elements on the top side of YRL039 and also components on the underside of the YRL040 PCB.  Those components likely to dissipate the most heat [motor drivers, PWM driver, amplifier and active outputs] are all towards the lower half of the PCB, which should receive forced convection from the fan.

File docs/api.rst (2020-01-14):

.. include global.rst
.. YRK API modules documentation

************
API Modules
************

The core API python modules are found in the ``yrk`` subfolder.

yrk.adc
-------
.. automodule:: yrk.adc
   :members:

yrk.audio
---------
.. automodule:: yrk.audio
  :members:

yrk.core
--------
.. automodule:: yrk.core
  :members:

yrk.display
-----------
.. automodule:: yrk.display
  :members:

yrk.gpio
--------
.. automodule:: yrk.gpio
  :members:

yrk.led
-------
.. automodule:: yrk.led
  :members:

yrk.motors
----------
.. automodule:: yrk.motors
  :members:

yrk.power
---------
.. automodule:: yrk.power
  :members:

yrk.pwm
-------
  .. automodule:: yrk.pwm
    :members:

yrk.settings
------------
.. automodule:: yrk.settings
  :members:

yrk.switch
----------
.. automodule:: yrk.switch
  :members:

yrk.utils
---------
.. automodule:: yrk.utils
  :members:

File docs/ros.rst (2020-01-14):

.. include global.rst
.. YRK ROS documentation

***********
YRK ROS API
***********

The ROS script, message and service files are found in the catkin workspace subfolder ``catwin_ws/src/yrk_ros``.

This can be quickly accessed from a terminal using the following ROS command::

  roscd yrk_ros

yrk_ros.adc_publisher
---------------------
.. automodule:: catkin_ws.src.yrk_ros.scripts.adc_publisher
  :members:

yrk_ros.button_publisher
------------------------
.. automodule:: catkin_ws.src.yrk_ros.scripts.button_publisher
  :members:

yrk_ros.display_server
----------------------
.. automodule:: catkin_ws.src.yrk_ros.scripts.display_server
  :members:

yrk_ros.led_server
------------------
.. automodule:: catkin_ws.src.yrk_ros.scripts.led_server
  :members:

yrk_ros.motor_server
--------------------
.. automodule:: catkin_ws.src.yrk_ros.scripts.motor_server
  :members:

yrk_ros.power_monitor
---------------------
.. automodule:: catkin_ws.src.yrk_ros.scripts.power_monitor
  :members:

yrk_ros.switched_output_server
------------------------------
.. automodule:: catkin_ws.src.yrk_ros.scripts.switched_output_server
  :members:

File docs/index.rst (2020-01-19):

.. include global.rst

.. YRK documentation master file

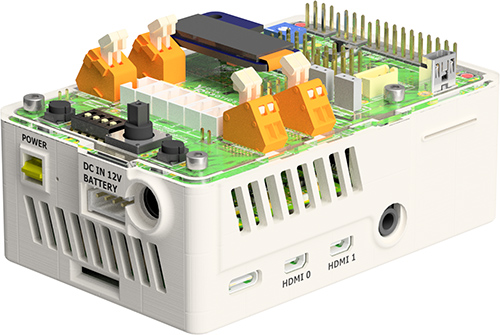
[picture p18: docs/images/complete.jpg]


.. toctree::
   :maxdepth: 2
   :caption: Contents:

   introduction
   hardware
   software
   api
   examples
   ros
   documents

*****
Index
*****

* :ref:`genindex`
* :ref:`modindex`
* :ref:`search`

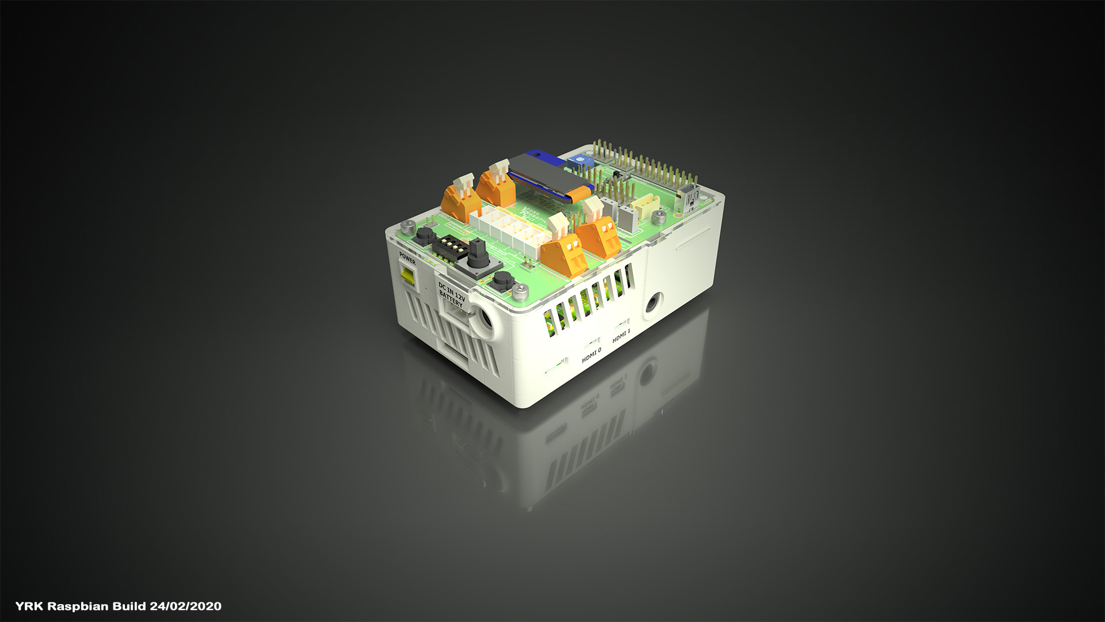
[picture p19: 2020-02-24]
pcb_documents/wallpaper.jpg

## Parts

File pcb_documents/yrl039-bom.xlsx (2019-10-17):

Part | Type | Value | Specs | Package | Manufacturer | Farnell | Other OC | Price
C1 | Capacitor | 10uF 25V | MLCC, min 20V, X7R pref. | C1210 |  | * |  | RS: 0.16each@50 172-1579 Taiyo Yden 1210 10uF 25V X7R Mouser cheaper still. Farnell 50p+
C2 | Capacitor | 10uF 25V | MLCC, min 20V, X7R pref. | C1210 |  | * |  | RS: 0.16each@50 172-1579 Taiyo Yden 1210 10uF 25V X7R Mouser cheaper still. Farnell 50p+
C3 | Capacitor | 10uF 25V | MLCC, min 20V, X7R pref. | C1210 |  | * |  | RS: 0.16each@50 172-1579 Taiyo Yden 1210 10uF 25V X7R Mouser cheaper still. Farnell 50p+
C4 | Capacitor | 10uF 25V | MLCC, min 20V, X7R pref. | C1210 |  | * |  | RS: 0.16each@50 172-1579 Taiyo Yden 1210 10uF 25V X7R Mouser cheaper still. Farnell 50p+
C5 | Capacitor | 1u 25V | MLCC, min 20V, X7R pref. | C0805
C6 | Capacitor | 3.3nF | MLCC | C0603
C7 | Capacitor | 3.3nF | MLCC | C0603
C8 | Capacitor | 1uF | MLCC | C0805
C9 | Capacitor | 47uF 10V | MLCC, min 8V, X7R pref. | C1210
C10 | Capacitor | 47uF 10V | MLCC, min 8V, X7R pref. | C1210
C11 | Capacitor | 100nF | MLCC | C0603 |  |  |  |  | Stock
C12 | Capacitor | 100nF | MLCC | C0603 |  |  |  |  | Stock
C13 | Capacitor | 1uF | MLCC | C0603
C14 | Capacitor | 100nF | MLCC | C0603 |  |  |  |  | Stock
C15 | Capacitor | 100nF | MLCC | C0603 |  |  |  |  | Stock
C16 | Capacitor | 100nF | MLCC | C0603 |  |  |  |  | Stock
C17 | Capacitor | 100nF | MLCC | C0603 |  |  |  |  | Stock
C18 | Capacitor | 100nF | MLCC | C0603 |  |  |  |  | Stock
C19 | Capacitor | 100nF | MLCC | C0603
F1 | Polyfuse | 1812L260/16 | 2.6A HC, 5A TC, 16V | F1812 | Littelfuse | 2786593 |  | 1.2
FAN | Fan | MF35060V2-1000U-A99 | 35x35x6mm 5V | 35x35x6mm | Sunon |  | Mouser: 369-MF35060V21UA99 | 9.75
J2-A | Connector |  |  |  | Samtec
J2-B | Connector | CONNECTOR-PAIRS |  | CONNECTOR-PAIRS | Samtec
J3 | Connector | RAPC722X | 2.1mm DC Socket | Through Hole | Switchcraft | 1608727 |  | 0.779
J4 | Connector | S4B-XH-A | 4-way RA XH Connector | 2.5mm Pitch RA TH | JST | 1516291 | RS: 820-1589 | 0.15 | MOQ 100@Farnell
LED1 | LED | HSMF-C165 | Bi-Colour LED | SMD0.8x1.6 | Broadcom | 8554587 |  | 0.33
LED2 | LED | HSMF-C165 | Bi-Colour LED | SMD0.8x1.6 | Broadcom | 8554587 |  | 0.33
LED3 | LED | HSMF-C165 | Bi-Colour LED | SMD0.8x1.6 | Broadcom | 8554587 |  | 0.33
PCB1 | Connector | RPI3 |  | RPI3
PZ1 | Sounder | PKMCS0909E4000 |  | 9mm Square | Murata | 2529461 |  | 1.1
Q1 | Transistor | FDV303N | N-MOS | FDV303N-SOT-23-NMOS | On Semi | 9845020 |  | 0.248
R1 | Resistor | 523k |  | R0603 | Panasonic | 2303294 |  | 0.0381
R2 | Resistor | 100k |  | R0603 |  |  |  |  | Stock
R3 | Resistor | 523k |  | R0603 | Panasonic | 2303294 |  | 0.0381
R4 | Resistor | 100k |  | R0603 |  |  |  |  | Stock
R5 | Resistor | 5m |  | R0805 |  | 2729138 |  | 0.39 | MOQ 10
R6 | Resistor | 5m |  | R0805 |  | 2729138 |  | 0.39 | MOQ 10
R7 | Resistor | 1K |  | R0603 |  |  |  |  | Stock
R8 | Resistor | 100 |  | R0603 |  |  |  |  | Stock
R9 | Resistor | 400K |  | R0603 |  | 2447366
R10 | Resistor | 100K |  | R0603 |  |  |  |  | Stock
R11 | Resistor | 10K |  | R0603 |  |  |  |  | Stock
R12 | Resistor | 10K |  | R0603 |  |  |  |  | Stock
R13 | Resistor | 400K |  | R0603 |  | 2447366
R14 | Resistor | 100K |  | R0603 |  |  |  |  | Stock
R15 | Resistor | 1M4 |  | R0603
R16 | Resistor | 100K |  | R0603 |  |  |  |  | Stock
RA1 | Resistor Array | CAY16-102J4LF | 1K 4-Element Array | 1206-RES-ARRAY | Bourns | 1770133 |  | 0.06
RA2 | Resistor Array | CAY16-102J4LF | 1K 4-Element Array | 1206-RES-ARRAY | Bourns | 1770133 |  | 0.06
SW1 | Switch | DTSM-32S-B | DTSM-3 Series | 6X3.5-SWITCH | Multicomp | 9471898 |  | 0.17 | MOQ 15 Farnell
SW2 | Switch | DTSM-32S-B | DTSM-3 Series | 6X3.5-SWITCH | Multicomp | 9471898 |  | 0.17 | MOQ 15 Farnell
U1 | Regulator | NCP718BSN330T1G | 2.5V-24V 3.3V Out LDO Reg ["GCH"] | TSOT-23-5 | On Semi |  |  |  | OOS Farnell [2mnth], 12-day RS [185-9270], 1 mnth mouser.
U2 | VR Module | TPS82130 |  | TPS82130-MODULE | Texas Inst. | N/A | RS: 133-0778 | 3.29 | Not yet stocked Farnell [3007470,3008331]
U3 | VR Module | TPS82130 |  | TPS82130-MODULE | Texas Inst. | N/A | RS: 133-0778 | 3.29 | Not yet stocked Farnell [3007470,3008331]
U4 | Protection IC | FR014H5JZ |  | FR014H5JZ | On Semi | 2322491 |  | 0.697
U5 | Temp Sensor | TC1046VNBTR | 6.25mV/C 0C=424mV | SOT-23 | Microchip | 1212685 |  | 0.49
U6 | CS Amplifier | INA2180A2IDGKT | A2 Version gain=50 | SOP65P490X110-9N | Texas Inst. | 2842971 |  | 0.662
U7 | Microcontroller | ATMEGA328P-AU |  | TQFP32-08 | Microchip | 1715486 |  | 1.5
X1 | Resonator | CSTCE8 8MHz Res. |  | RESONATOR | Murata | N/A | RS: 721-4827 283-961 Mouser: 81-CSTCE8M00GH5C99R0

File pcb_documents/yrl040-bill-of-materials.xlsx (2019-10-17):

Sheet: By Component
Part | Quantity | Value | Description | Package | Farnell | Notes
C1,7,9,14-19,22,23,26,27,29-33,36-38 | 21 | 100n | Capacitor 0603 X5R+ 16V+ | C0603
C2 | 1 | 33n | Capacitor 0603 X5R+ 16V+ | C0603
C3,6,8 | 3 | 4.7uF | Capacitor 0805 X5R+ 6.3V+ | C0805
C4,5 | 2 | 10n | Capacitor 0603 X5R+ 16V+ | C0603
C10-12,20,21,24,25 | 7 | 10uF | Capacitor 1206 X5R+ 6.3V+ 10uF+ | C1206
C13 | 1 | 200p | Capacitor 0603 C0G 10V+ | C0603
C28 | 1 | 1u | Capacitor 0603 X5R+ 6.3V+ | C0603
C34,35 | 2 | 22pF | Capacitor 0603 C0G 10V+ | C0603
F1-5 | 5 | 1A | Fuse 0603 1A Fast Acting 20V+ | F0603 | 1337408
IC1 | 1 | FT232RL | USB:Serial Interface | SSOP28 | 1146032
IC2 | 1 | ATMEGA328P-AU | Microcontroller | TQFP32-08 | 1715486
J1 |  | CONNECTOR-PAIRS | CONNECTOR-PAIRS | CONNECTOR-PAIRS
J2-5 | 4 | Picoblade 4-Pin | Picoblade 4-pin TH Header | 4x1.25mm | 9733060
J6 |  | YRL012-EXPORTED_ADA-128X32-DISPLAY | YRL012-EXPORTED_ADA-128X32-DISPLAY | YRL012-EXPORTED_I2C_PI_OLED
J7 |  | SERVO_CONNECTION_BLOCK | SERVO_CONNECTION_BLOCK | SERVO_BLOCK_8X2
J8,9,16,17 | 4 | 233-502 | Wago 2-Way Terminal Block | 2.54mmx2 | 1777096
J10-15 | 6 | SHARP-SENSOR | SHARP-SENSOR | JST-3PIN-PH
J18 | 1 | MINI-USB | MINI-USB | MINIUSB-VERT-1841175 | 1841175
J19 |  | ARDUINO-CONNECTORS | ARDUINO-CONNECTORS | 2X10-PIN-ARDUINO
J21 |  | MOLEX3PIN-9979620 | MOLEX3PIN-9979620 | MOLEX-3PIN-9979620
J22 |  | GPIO-8PIN | GPIO-8PIN | 4X2X0.1-GPIO"
J23,24 | 2 | SPO-2-PIN-HEADER | SPO-2-PIN-HEADER | 2-PIN-SPO
LED1-4 | 4 | KPTL LED | Kingbright Reverse Mount LED, Yellow | LED1206-REV | 2217902
LED5,6 | 2 | RGB LED | Bourns ASMB-MTB0-0A3A2 RGB LED | LED2.4mm | 2401105
LED7,8,12 | 3 | KPTL LED | Kingbright Reverse Mount LED, Red | LED1206-REV | 2217900
LED9-11 | 3 | SML825 LED | ROHM SML-825MVWT86 Bi-Colour Rev. Mount LED | LED1305-REV | 2908899
MIC1 | 1 | SPH0645LM4H-B | MEMS Microphone |  |  | MOUSER: 721-SPH0645LM4H-B
Q1,2 | 2 | BSR802N-MOSFET-2443469 | BSR802N-MOSFET-2443469 | BSR802N-NMOS | 2443469
R1 | 1 | 270 | Resistor 0603 | R0603
R2 | 1 | 150 | Resistor 0603 | R0603
R3 | 1 | 4.7k | Resistor 0603 | R0603
R4-6,19 | 4 | 100K | Resistor 0603 | R0603
R7,20-24,26,30 | 8 | 10K | Resistor 0603 | R0603
R8-10 | 3 | 51 | Resistor 0603 | R0603
R11-18 | 8 | 500m | Current Sense Resistor 0805 250mW+ | R0805 | 1506145
R25,31 | 2 | 1K | Resistor 0603 | R0603
R27 | 1 | 220 | Resistor 0603 | R0603
R28,29 | 2 | 470 | Resistor 0603 | R0603
RA1-4 | 4 | 2k2 | Resistor Array 1206 | RA1206-4 | 1770134
RA5,10,13 | 3 | 1K | Resistor Array 1206 | RA1206-4 | 1770133
RA6-9 | 4 | 220 | Resistor Array 1206 | RA1206-4 | 2321743
RA11,12 | 2 | 100 | Resistor Array 1206 | RA1206-4 | 1770131
SW1 | 1 | 4-Way DIP Switch | SM 4-Way DIP [1825058-7] | 4x0.1" | 2468733
SW2,3 | 2 | Push Button | Panasonic EVPAS Series | 6x6.1mm | 2425608
SW4 | 1 | Nav Switch | ALPS SKQUCAA010 |  |  | OBSOLETE! Replace with SM version in next PCB revision
SW5 | 1 | DPDT Switch | C&K JS202011CQN | 0.1" Pitch TH | 2320018
SW6 | 1 | SWITCH-9471898 | SWITCH-9471898 | 6X3.5-SWITCH
U1 | 1 | MCP1824T-3302E/OT | MCP1824T-3302E/OT | SOT95P270X145-5N
U2 | 1 | PCA9548APWR | PCA9548APWR | SOP65P640X120-24N
U3 | 1 | TPA2005D1DGN | TI Audio Amplifier | MSOP-8 | 2075395
U4,13 | 2 | PCA9555PW,118 | GPIO Expander, NXP or TI | TSSOP-24 | 8906084
U5 | 1 | PCA9685PW | NXP LED {PWM} Driver | TSSOP-28 | 1854074
U6 | 1 | ADS7830IPWTG4 | Octal ADC | TSSOP-16 | 1180129
U7-10 | 4 | DRV8830DGQR | TI Motor Driver | TSSOP-10 | 1863106
U11 | 1 | SN74AHCT1G04DCKT | Inverter, 1 input | SC-70-5 | 1902169 | New order code soon
U12 | 1 | SN74LVC2G126DCUT-1741035 | Buffer | VSSOP-8 |  | No longer stocked @ Farnell. MOUSER: 595-SN74LVC2G126DCUR
U14 | 1 | TCA6507PW | TI LED Driver | TSSOP-14 | 1647813 | Till stock exhausted
U15 | 1 | BNO055 | MICROBUILDER_BNO055 | MICROBUILDER_BNO055 |  | MOUSER: 262-BNO055
VR1 | 1 | 200K Pot | 3386F-1-204TLF | TH | 9354670
X1,2,4 | 3 | CON-MOLEX_87758-0216 | CON-MOLEX_87758-0216 | CON-MOLEX_87758-0216
X3 | 1 | CSTCE16 16MHz Res. | 0011_CSTCE16M0V53-R0 | RESONATOR |  | OBSOLETE, None at Farnell
X5 | 1 | 32.768kHz | SMD Crystall | CRYSTAL-2X1.2 | 2819313

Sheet: By Part Number
Part | Value | Description | Package | Farnell | Notes
C1 | 100n | Capacitor 0603 X5R+ 16V+ | C0603
C2 | 33n | Capacitor 0603 X5R+ 16V+ | C0603
C3 | 4.7uF | Capacitor 0805 X5R+ 6.3V+ | C0805
C4 | 10n | Capacitor 0603 X5R+ 16V+ | C0603
C5 | 10n | Capacitor 0603 X5R+ 16V+ | C0603
C6 | 4.7uF | Capacitor 0805 X5R+ 6.3V+ | C0805
C7 | 100n | Capacitor 0603 X5R+ 16V+ | C0603
C8 | 4.7uF | Capacitor 0805 X5R+ 6.3V+ | C0805
C9 | 100n | Capacitor 0603 X5R+ 16V+ | C0603
C10 | 10uF | Capacitor 1206 X5R+ 6.3V+ 10uF+ | C1206
C11 | 10uF | Capacitor 1206 X5R+ 6.3V+ 10uF+ | C1206
C12 | 10uF | Capacitor 1206 X5R+ 6.3V+ 10uF+ | C1206
C13 | 200p | Capacitor 0603 C0G 10V+ | C0603
C14 | 100n | Capacitor 0603 X5R+ 16V+ | C0603
C15 | 100n | Capacitor 0603 X5R+ 16V+ | C0603
C16 | 100n | Capacitor 0603 X5R+ 16V+ | C0603
C17 | 100n | Capacitor 0603 X5R+ 16V+ | C0603
C18 | 100n | Capacitor 0603 X5R+ 16V+ | C0603
C19 | 100n | Capacitor 0603 X5R+ 16V+ | C0603
C20 | 10uF | Capacitor 1206 X5R+ 6.3V+ 10uF+ | C1206
C21 | 10uF | Capacitor 1206 X5R+ 6.3V+ 10uF+ | C1206
C22 | 100n | Capacitor 0603 X5R+ 16V+ | C0603
C23 | 100n | Capacitor 0603 X5R+ 16V+ | C0603
C24 | 10uF | Capacitor 1206 X5R+ 6.3V+ 10uF+ | C1206
C25 | 10uF | Capacitor 1206 X5R+ 6.3V+ 10uF+ | C1206
C26 | 100n | Capacitor 0603 X5R+ 16V+ | C0603
C27 | 100n | Capacitor 0603 X5R+ 16V+ | C0603
C28 | 1u | Capacitor 0603 X5R+ 6.3V+ | C0603
C29 | 100n | Capacitor 0603 X5R+ 16V+ | C0603
C30 | 100n | Capacitor 0603 X5R+ 16V+ | C0603
C31 | 100n | Capacitor 0603 X5R+ 16V+ | C0603
C32 | 100n | Capacitor 0603 X5R+ 16V+ | C0603
C33 | 100n | Capacitor 0603 X5R+ 16V+ | C0603
C34 | 22pF | Capacitor 0603 C0G 10V+ | C0603
C35 | 22pF | Capacitor 0603 C0G 10V+ | C0603
C36 | 100n | Capacitor 0603 X5R+ 16V+ | C0603
C37 | 100n | Capacitor 0603 X5R+ 16V+ | C0603
C38 | 100n | Capacitor 0603 X5R+ 16V+ | C0603
F1 | 1A | Fuse 0603 1A Fast Acting 20V+ | F0603 | 1337408
F2 | 1A | Fuse 0603 1A Fast Acting 20V+ | F0603 | 1337408
F3 | 1A | Fuse 0603 1A Fast Acting 20V+ | F0603 | 1337408
F4 | 1A | Fuse 0603 1A Fast Acting 20V+ | F0603 | 1337408
F5 | 1A | Fuse 0603 1A Fast Acting 20V+ | F0603 | 1337408
IC1 | FT232RL | USB:Serial Interface | SSOP28 | 1146032
IC2 | ATMEGA328P-AU | Microcontroller | TQFP32-08 | 1715486
J1 | CONNECTOR-PAIRS | CONNECTOR-PAIRS | CONNECTOR-PAIRS
J2 | Picoblade 4-Pin | Picoblade 4-pin TH Header | 4x1.25mm | 9733060
J3 | Picoblade 4-Pin | Picoblade 4-pin TH Header | 4x1.25mm | 9733060
J4 | Picoblade 4-Pin | Picoblade 4-pin TH Header | 4x1.25mm | 9733060
J5 | Picoblade 4-Pin | Picoblade 4-pin TH Header | 4x1.25mm | 9733060
J6 | YRL012-EXPORTED_ADA-128X32-DISPLAY | YRL012-EXPORTED_ADA-128X32-DISPLAY | YRL012-EXPORTED_I2C_PI_OLED
J7 | SERVO_CONNECTION_BLOCK | SERVO_CONNECTION_BLOCK | SERVO_BLOCK_8X2
J8 | 233-502 | Wago 2-Way Terminal Block | 2.54mmx2 | 1777096
J9 | 233-502 | Wago 2-Way Terminal Block | 2.54mmx2 | 1777096
J10 | SHARP-SENSOR | SHARP-SENSOR | JST-3PIN-PH
J11 | SHARP-SENSOR | SHARP-SENSOR | JST-3PIN-PH
J12 | SHARP-SENSOR | SHARP-SENSOR | JST-3PIN-PH
J13 | SHARP-SENSOR | SHARP-SENSOR | JST-3PIN-PH
J14 | SHARP-SENSOR | SHARP-SENSOR | JST-3PIN-PH
J15 | SHARP-SENSOR | SHARP-SENSOR | JST-3PIN-PH
J16 | 233-502 | Wago 2-Way Terminal Block | 2.54mmx2 | 1777096
J17 | 233-502 | Wago 2-Way Terminal Block | 2.54mmx2 | 1777096
J18 | MINI-USB | MINI-USB | MINIUSB-VERT-1841175
J19 | ARDUINO-CONNECTORS | ARDUINO-CONNECTORS | 2X10-PIN-ARDUINO
J21 | MOLEX3PIN-9979620 | MOLEX3PIN-9979620 | MOLEX-3PIN-9979620
J22 | GPIO-8PIN | GPIO-8PIN | 4X2X0.1-GPIO"
J23 | SPO-2-PIN-HEADER | SPO-2-PIN-HEADER | 2-PIN-SPO
J24 | SPO-2-PIN-HEADER | SPO-2-PIN-HEADER | 2-PIN-SPO
LED1 | KPTL LED | Kingbright Reverse Mount LED, Yellow | LED1206-REV | 2217902
LED2 | KPTL LED | Kingbright Reverse Mount LED, Yellow | LED1206-REV | 2217902
LED3 | KPTL LED | Kingbright Reverse Mount LED, Yellow | LED1206-REV | 2217902
LED4 | KPTL LED | Kingbright Reverse Mount LED, Yellow | LED1206-REV | 2217902
LED5 | RGB LED | Bourns ASMB-MTB0-0A3A2 RGB LED | LED2.4mm | 2401105
LED6 | RGB LED | Bourns ASMB-MTB0-0A3A2 RGB LED | LED2.4mm | 2401105
LED7 | KPTL LED | Kingbright Reverse Mount LED, Red | LED1206-REV | 2217900
LED8 | KPTL LED | Kingbright Reverse Mount LED, Red | LED1206-REV | 2217900
LED9 | SML825 LED | ROHM SML-825MVWT86 Bi-Colour Rev. Mount LED | LED1305-REV | 2908899
LED10 | SML825 LED | ROHM SML-825MVWT86 Bi-Colour Rev. Mount LED | LED1305-REV | 2908899
LED11 | SML825 LED | ROHM SML-825MVWT86 Bi-Colour Rev. Mount LED | LED1305-REV | 2908899
LED12 | KPTL LED | Kingbright Reverse Mount LED, Red | LED1206-REV | 2217900
MIC1 | MICROBUILDER_MIC_I2S_SPH0645 | MICROBUILDER_MIC_I2S_SPH0645 | MICROBUILDER_SPH0645LM4H
Q1 | BSR802N-MOSFET-2443469 | BSR802N-MOSFET-2443469 | BSR802N-NMOS
Q2 | BSR802N-MOSFET-2443469 | BSR802N-MOSFET-2443469 | BSR802N-NMOS
R1 | 270 | Resistor 0603 | R0603
R2 | 150 | Resistor 0603 | R0603
R3 | 4.7k | Resistor 0603 | R0603
R4 | 100K | Resistor 0603 | R0603
R5 | 100K | Resistor 0603 | R0603
R6 | 100K | Resistor 0603 | R0603
R7 | 10K | Resistor 0603 | R0603
R8 | 51 | Resistor 0603 | R0603
R9 | 51 | Resistor 0603 | R0603
R10 | 51 | Resistor 0603 | R0603
R11 | 500m | Current Sense Resistor 0805 250mW+ | R0805 | 1506145
R12 | 500m | Current Sense Resistor 0805 250mW+ | R0805 | 1506145
R13 | 500m | Current Sense Resistor 0805 250mW+ | R0805 | 1506145
R14 | 500m | Current Sense Resistor 0805 250mW+ | R0805 | 1506145
R15 | 500m | Current Sense Resistor 0805 250mW+ | R0805 | 1506145
R16 | 500m | Current Sense Resistor 0805 250mW+ | R0805 | 1506145
R17 | 500m | Current Sense Resistor 0805 250mW+ | R0805 | 1506145
R18 | 500m | Current Sense Resistor 0805 250mW+ | R0805 | 1506145
R19 | 100K | Resistor 0603 | R0603
R20 | 10K | Resistor 0603 | R0603
R21 | 10K | Resistor 0603 | R0603
R22 | 10K | Resistor 0603 | R0603
R23 | 10K | Resistor 0603 | R0603
R24 | 10K | Resistor 0603 | R0603
R25 | 1K | Resistor 0603 | R0603
R26 | 10K | Resistor 0603 | R0603
R27 | 220 | Resistor 0603 | R0603
R28 | 470 | Resistor 0603 | R0603
R29 | 470 | Resistor 0603 | R0603
R30 | 10K | Resistor 0603 | R0603
R31 | 1K | Resistor 0603 | R0603
RA1 | 2k2 | Resistor Array 1206 | RA1206-4 | 1770134
RA2 | 2k2 | Resistor Array 1206 | RA1206-4 | 1770134
RA3 | 2k2 | Resistor Array 1206 | RA1206-4 | 1770134
RA4 | 2k2 | Resistor Array 1206 | RA1206-4 | 1770134
RA5 | 1K | Resistor Array 1206 | RA1206-4 | 1770133
RA6 | 220 | Resistor Array 1206 | RA1206-4 | 2321743
RA7 | 220 | Resistor Array 1206 | RA1206-4 | 2321743
RA8 | 220 | Resistor Array 1206 | RA1206-4 | 2321743
RA9 | 220 | Resistor Array 1206 | RA1206-4 | 2321743
RA10 | 1K | Resistor Array 1206 | RA1206-4 | 1770133
RA11 | 100 | Resistor Array 1206 | RA1206-4 | 1770131
RA12 | 100 | Resistor Array 1206 | RA1206-4 | 1770131
RA13 | 1K | Resistor Array 1206 | RA1206-4 | 1770133
SW1 | 4-Way DIP Switch | SM 4-Way DIP [1825058-7] | 4x0.1" | 2468733
SW2 | Push Button | Panasonic EVPAS Series | 6x6.1mm | 2425608
SW3 | Push Button | Panasonic EVPAS Series | 6x6.1mm | 2425608
SW4 | Nav Switch | ALPS SKQUCAA010 |  |  | OBSOLETE! Replace with SM version in next PCB revision
SW5 | DPDT Switch | C&K JS202011CQN | 0.1" Pitch TH | 2320018
SW6 | SWITCH-9471898 | SWITCH-9471898 | 6X3.5-SWITCH
U1 | MCP1824T-3302E/OT | MCP1824T-3302E/OT | SOT95P270X145-5N
U2 | PCA9548APWR | PCA9548APWR | SOP65P640X120-24N
U3 | TPA2005D1DGN | TI Audio Amplifier | MSOP-8 | 2075395
U4 | PCA9555PW,118 | NXP or TI | TSSOP-24 | 8906084
U5 | PCA9685PW | NXP LED {PWM} Driver | TSSOP-28 | 1854074
U6 | ADS7830IPWTG4 | Octal ADC | TSSOP-16 | 1180129
U7 | DRV8830DGQR | TI Motor Driver | TSSOP-10 | 1863106
U8 | DRV8830DGQR | TI Motor Driver | TSSOP-10 | 1863106
U9 | DRV8830DGQR | TI Motor Driver | TSSOP-10 | 1863106
U10 | DRV8830DGQR | TI Motor Driver | TSSOP-10 | 1863106
U11 | SN74AHCT1G04DCKT | Inverter, 1 input | SC-70-5 | 1902169 | New order code soon
U12 | SN74LVC2G126DCUT-1741035 | Buffer | VSSOP-8 |  | No longer stocked @ Farnell
U13 | PCA9555PW,118 | GPIO Expander, NXP or TI | TSSOP-24 | 8906084
U14 | TCA6507PW | TI LED Driver | TSSOP-14 | 1647813 | Till stock exhausted
U15 | BNO055 | MICROBUILDER_BNO055 | MICROBUILDER_BNO055
VR1 | 200K Pot | 3386F-1-204TLF | TH | 9354670
X1 | CON-MOLEX_87758-0216 | CON-MOLEX_87758-0216 | CON-MOLEX_87758-0216
X2 | CON-MOLEX_87758-0216 | CON-MOLEX_87758-0216 | CON-MOLEX_87758-0216
X3 | CSTCE16 16MHz Res. | 0011_CSTCE16M0V53-R0 | RESONATOR |  | OBSOLETE, None at Farnell
X4 | CON-MOLEX_87758-0216 | CON-MOLEX_87758-0216 | CON-MOLEX_87758-0216
X5 | 32.768kHz | SMD Crystall | CRYSTAL-2X1.2 | 2819313

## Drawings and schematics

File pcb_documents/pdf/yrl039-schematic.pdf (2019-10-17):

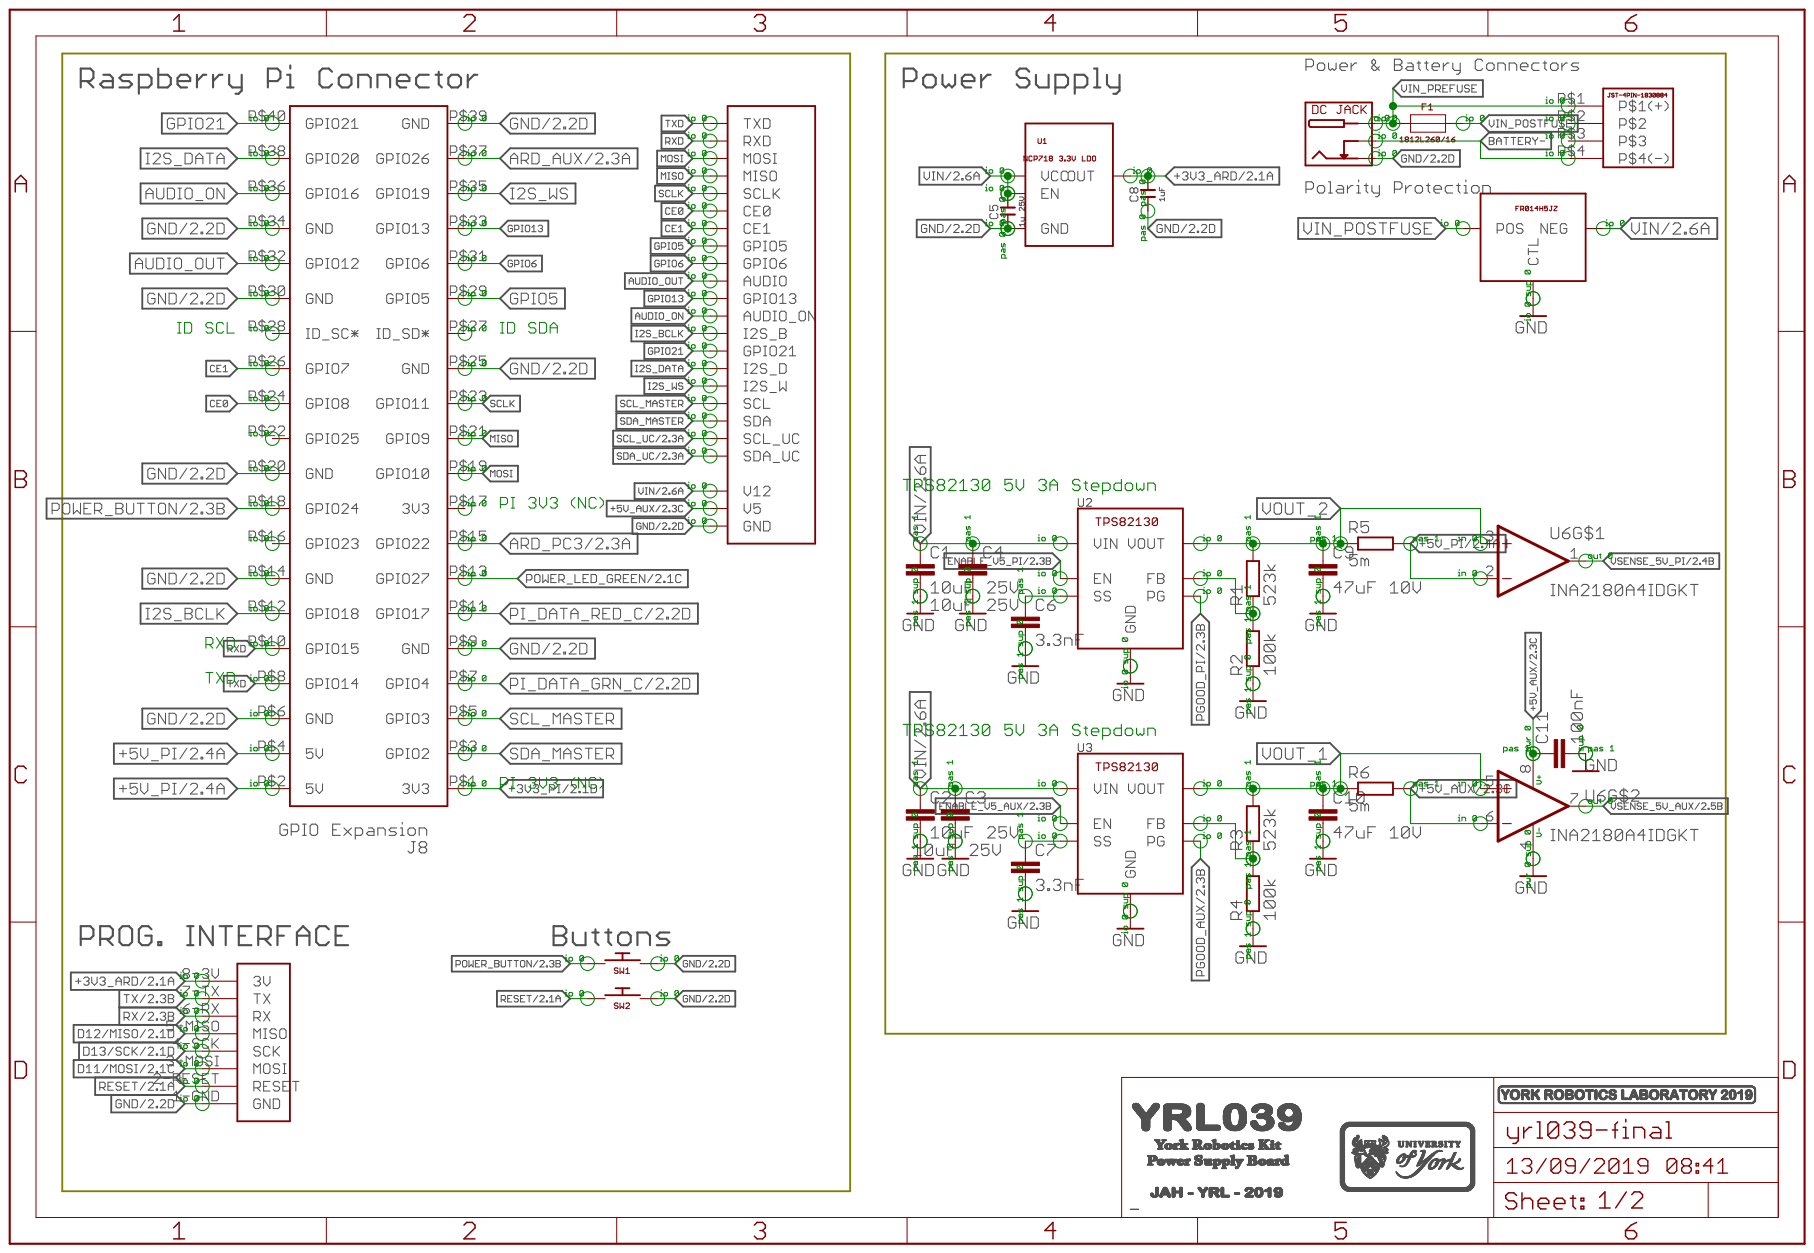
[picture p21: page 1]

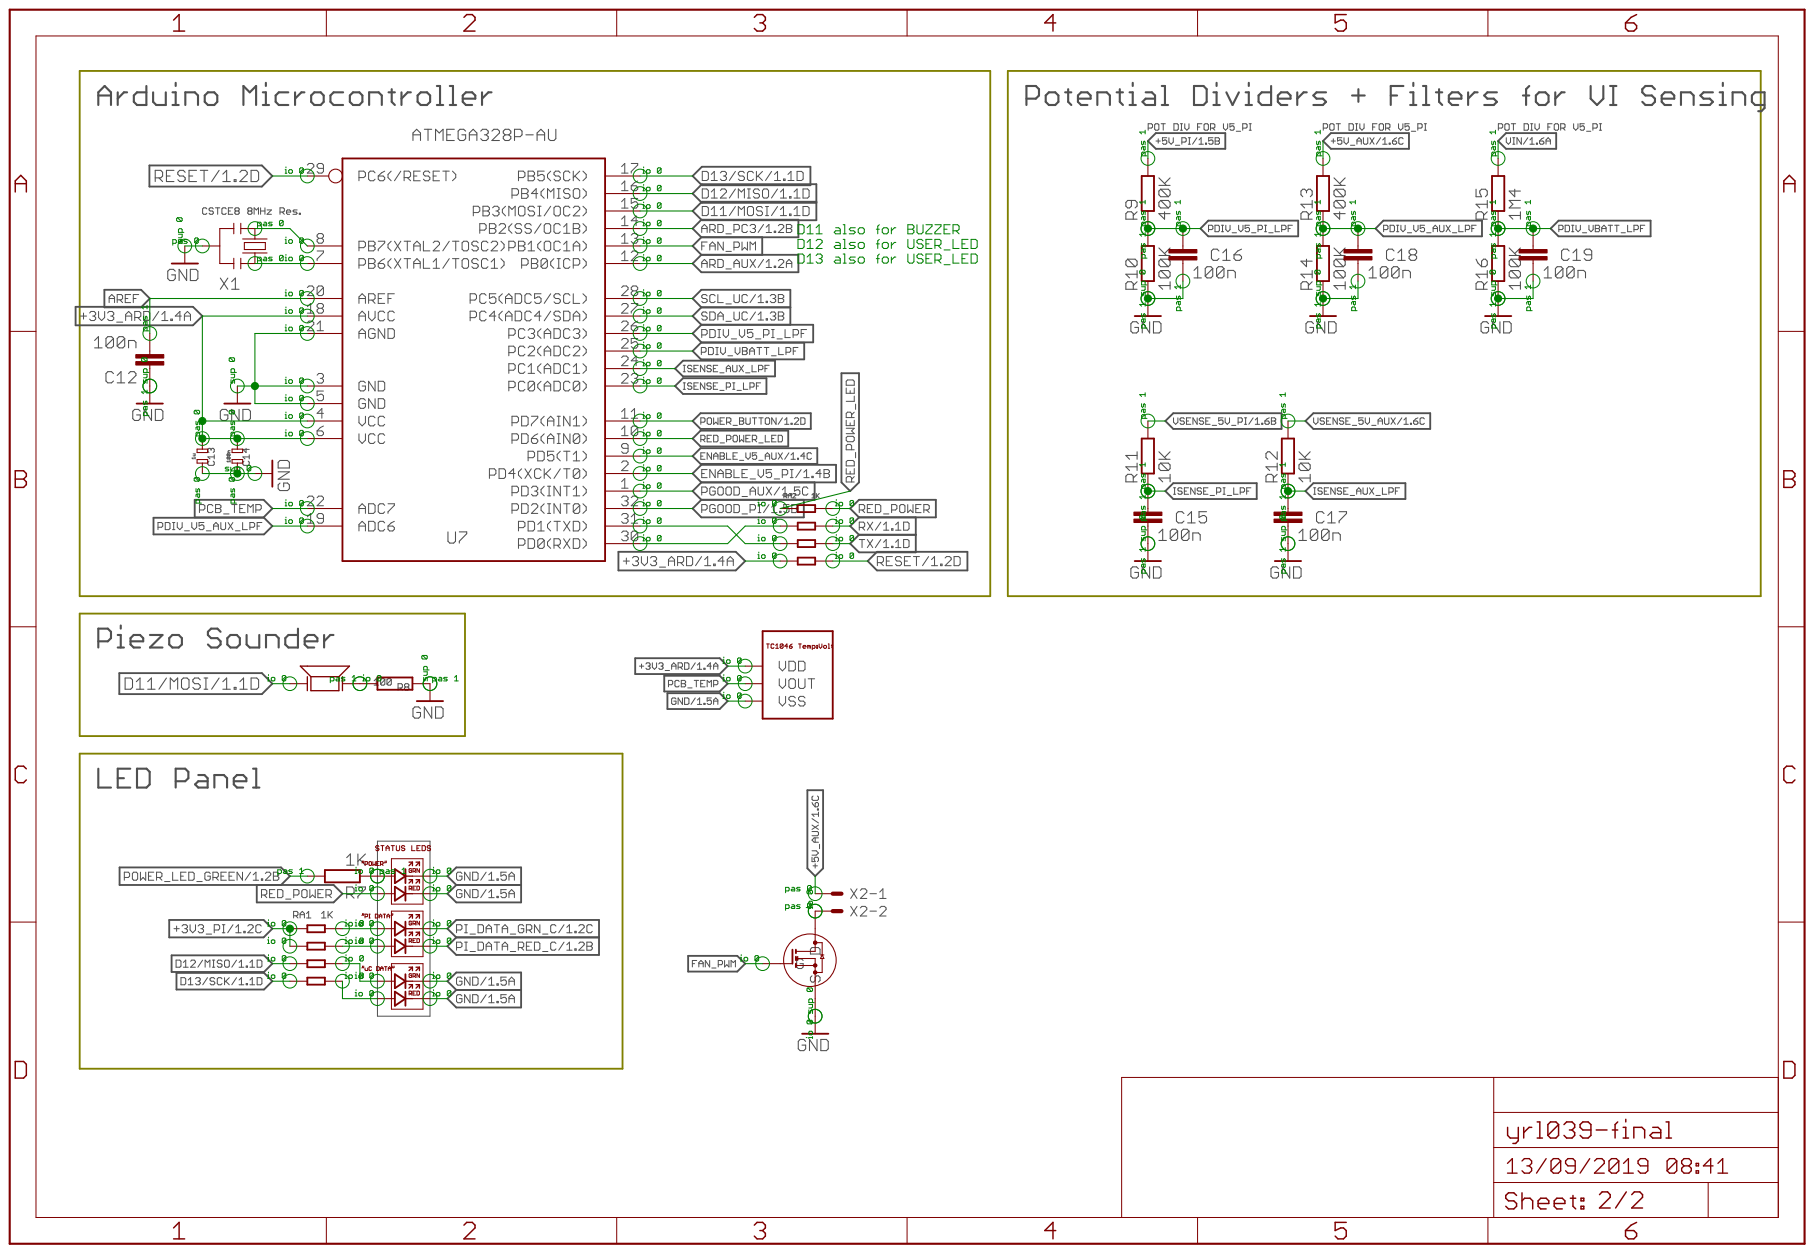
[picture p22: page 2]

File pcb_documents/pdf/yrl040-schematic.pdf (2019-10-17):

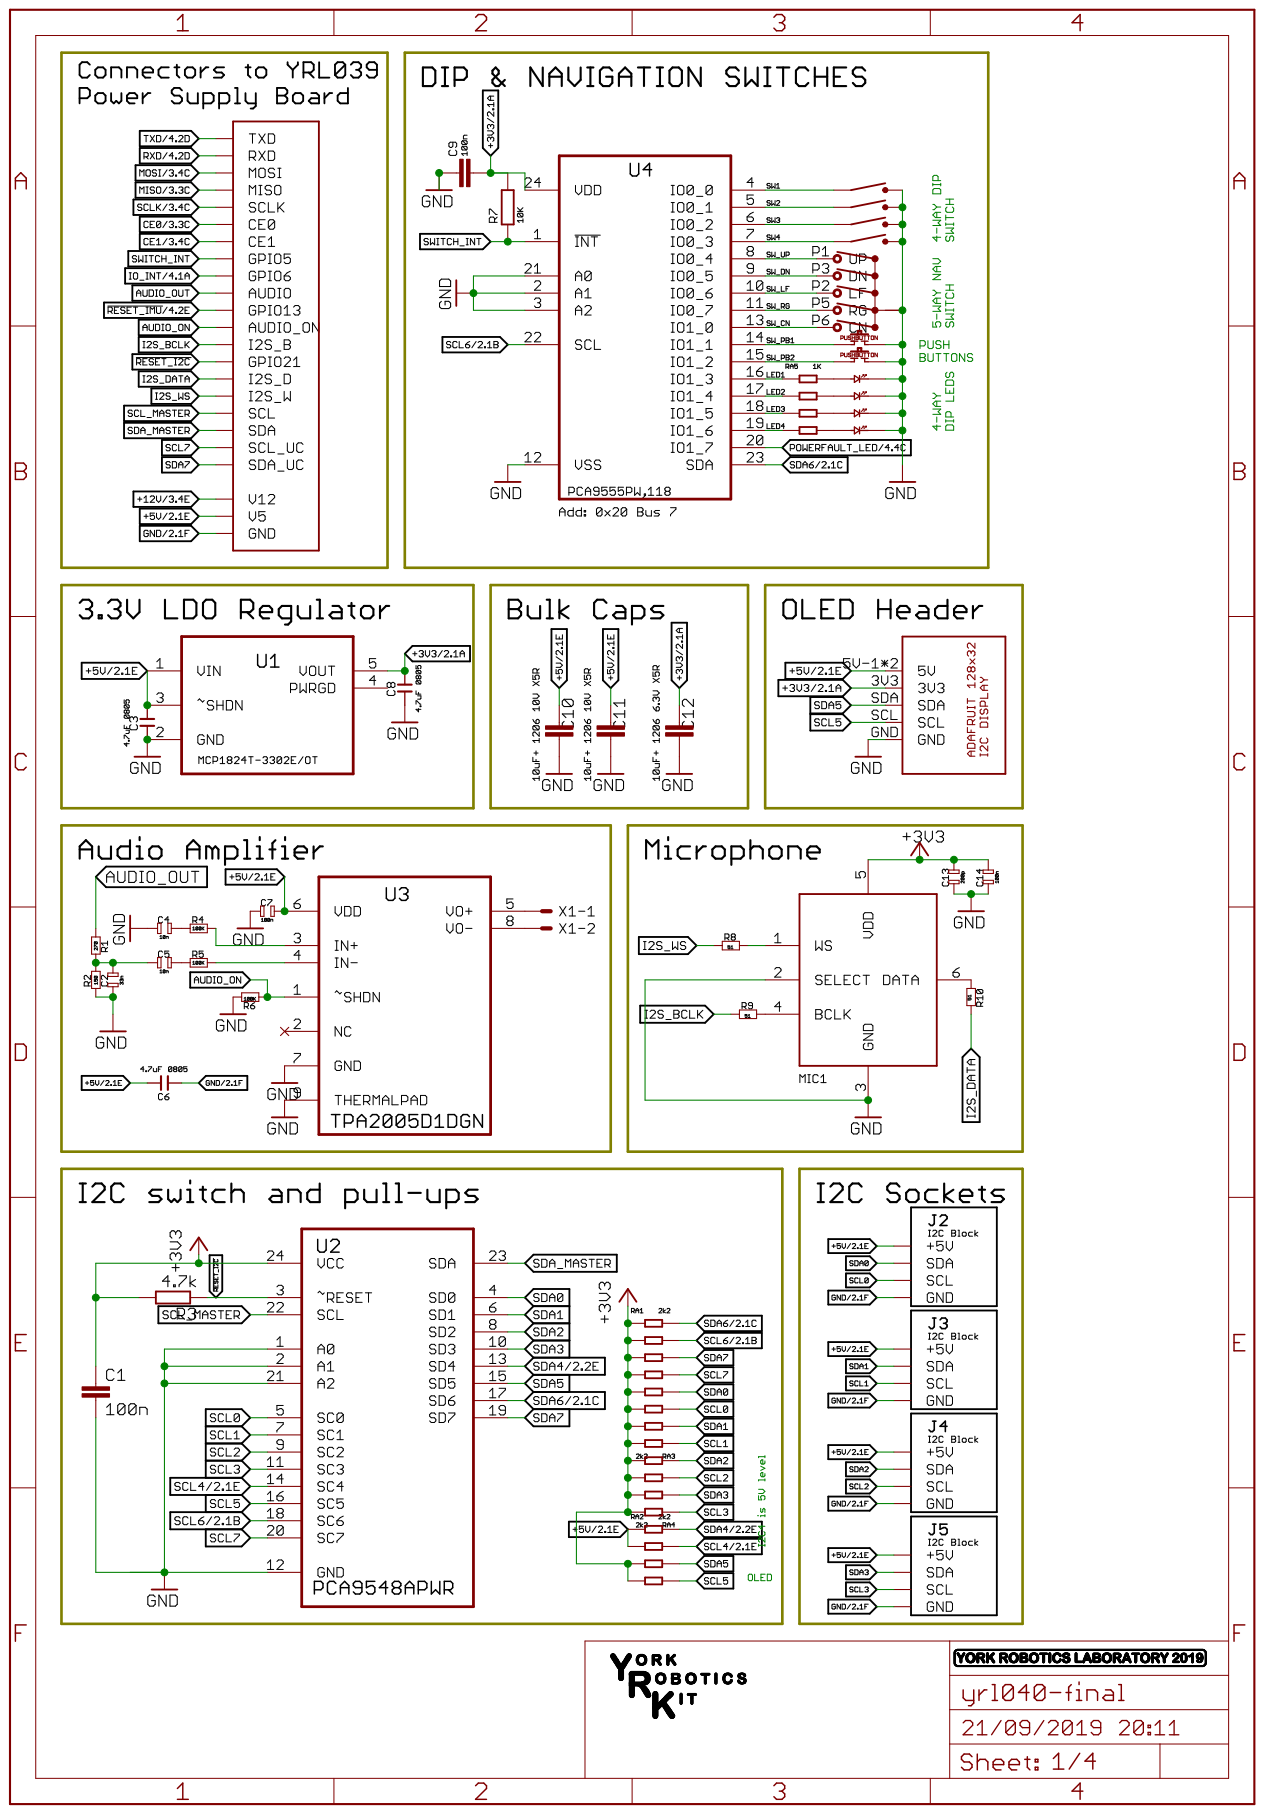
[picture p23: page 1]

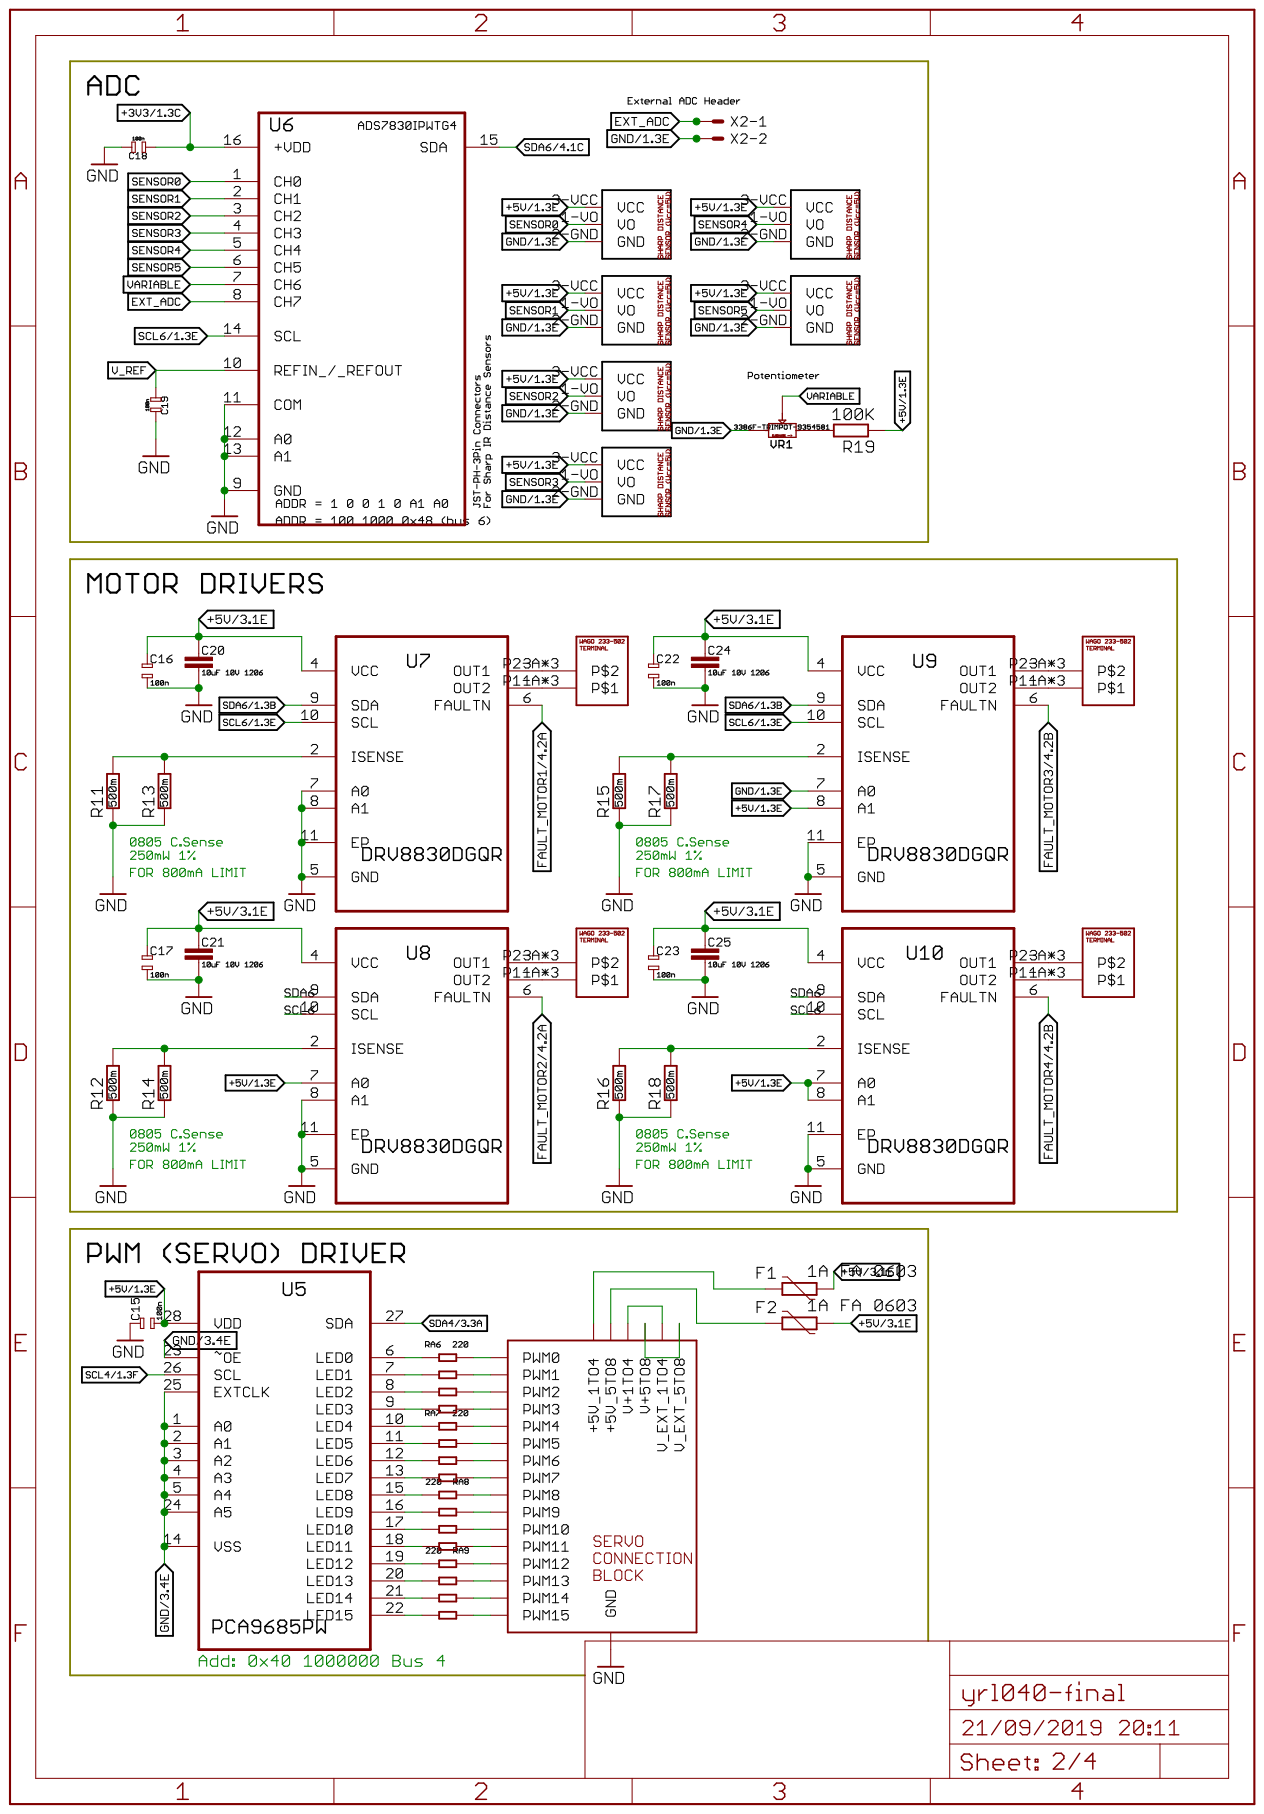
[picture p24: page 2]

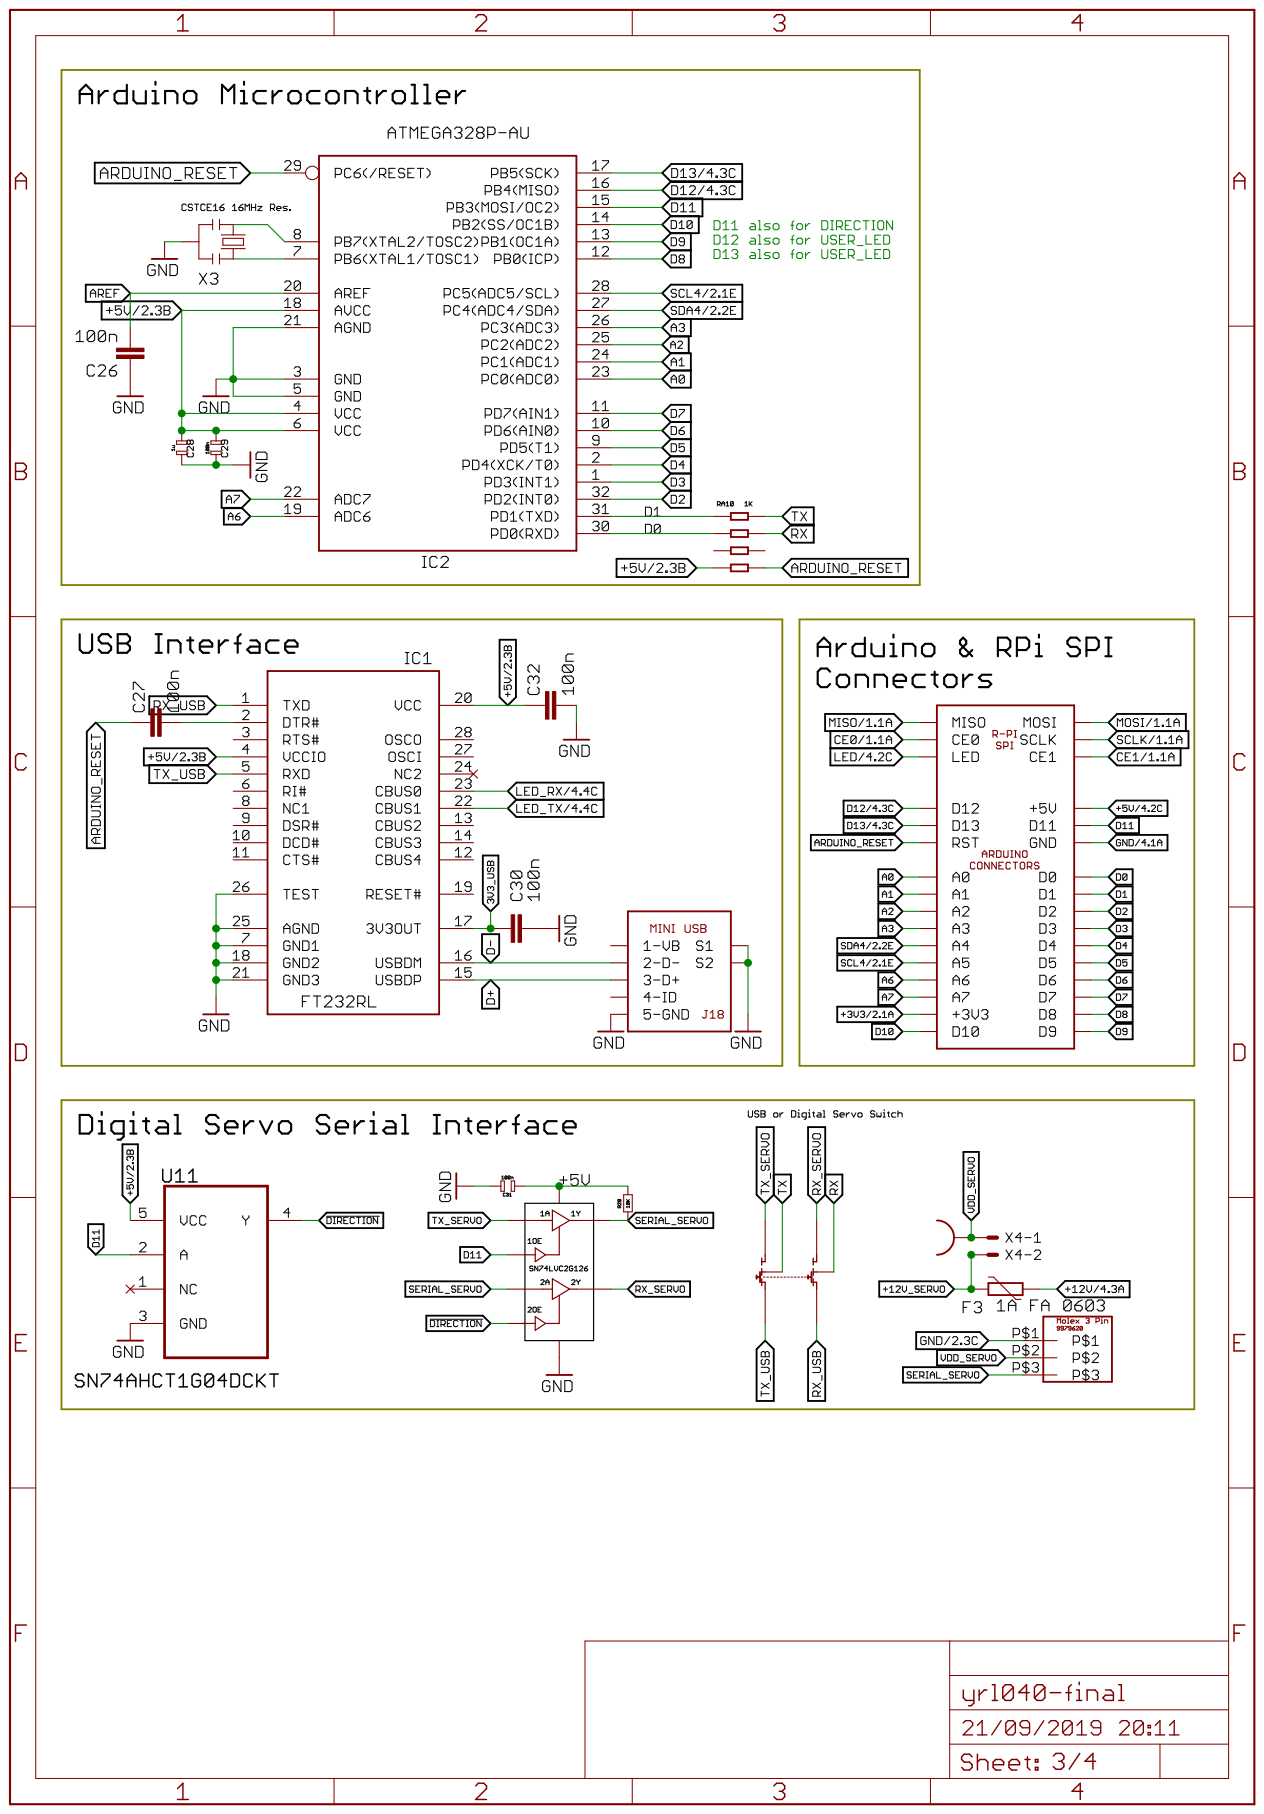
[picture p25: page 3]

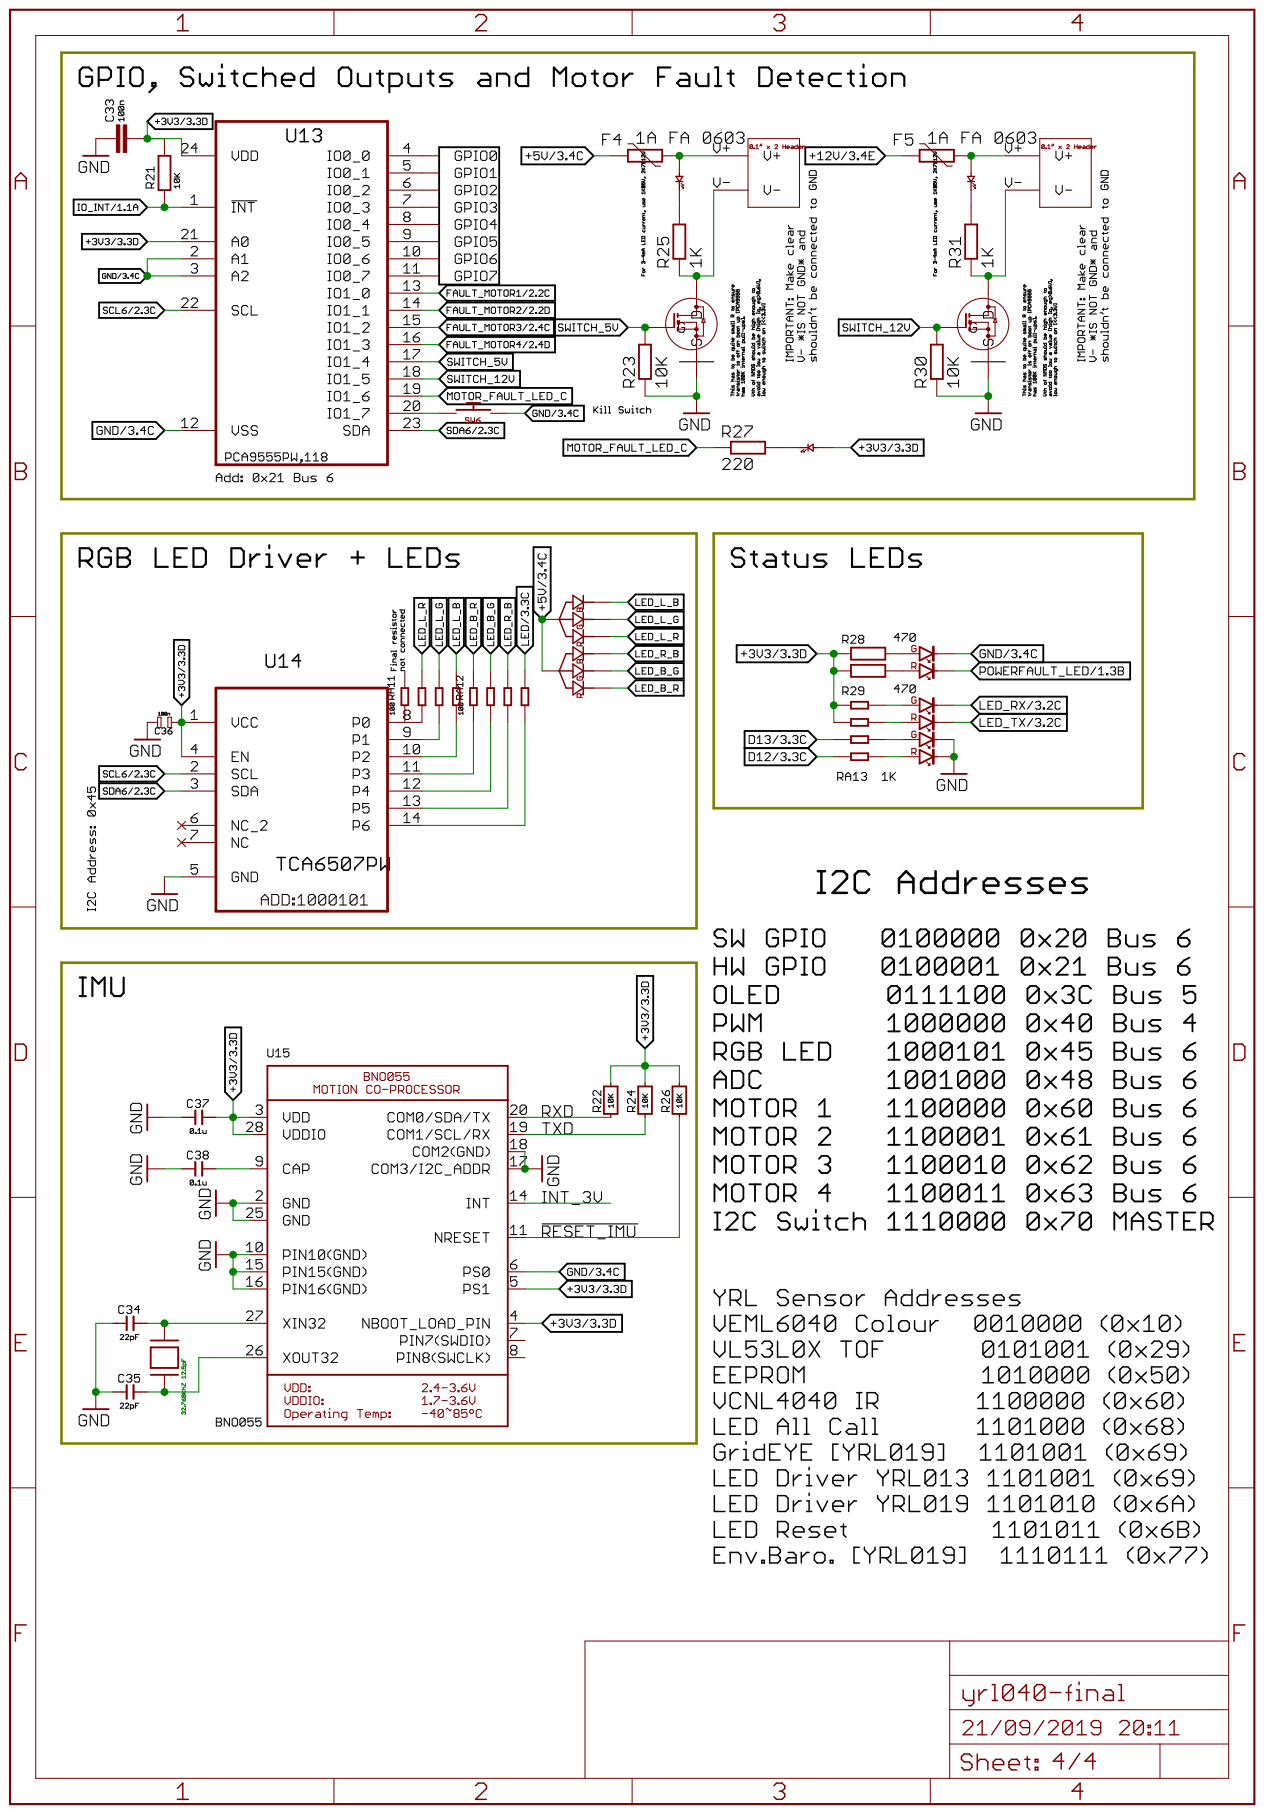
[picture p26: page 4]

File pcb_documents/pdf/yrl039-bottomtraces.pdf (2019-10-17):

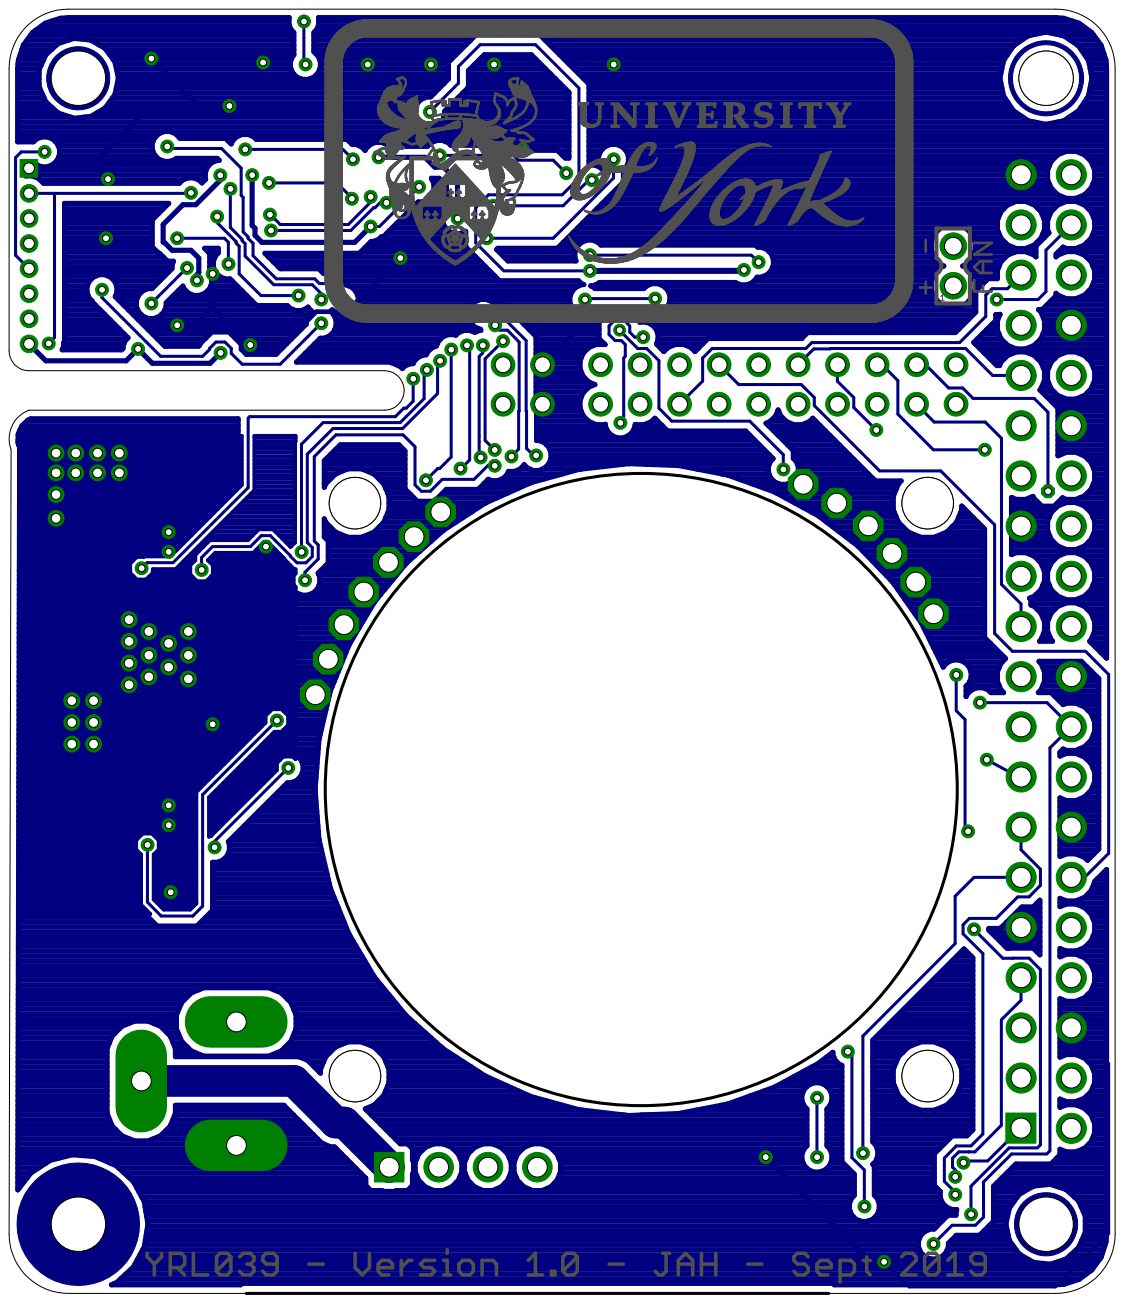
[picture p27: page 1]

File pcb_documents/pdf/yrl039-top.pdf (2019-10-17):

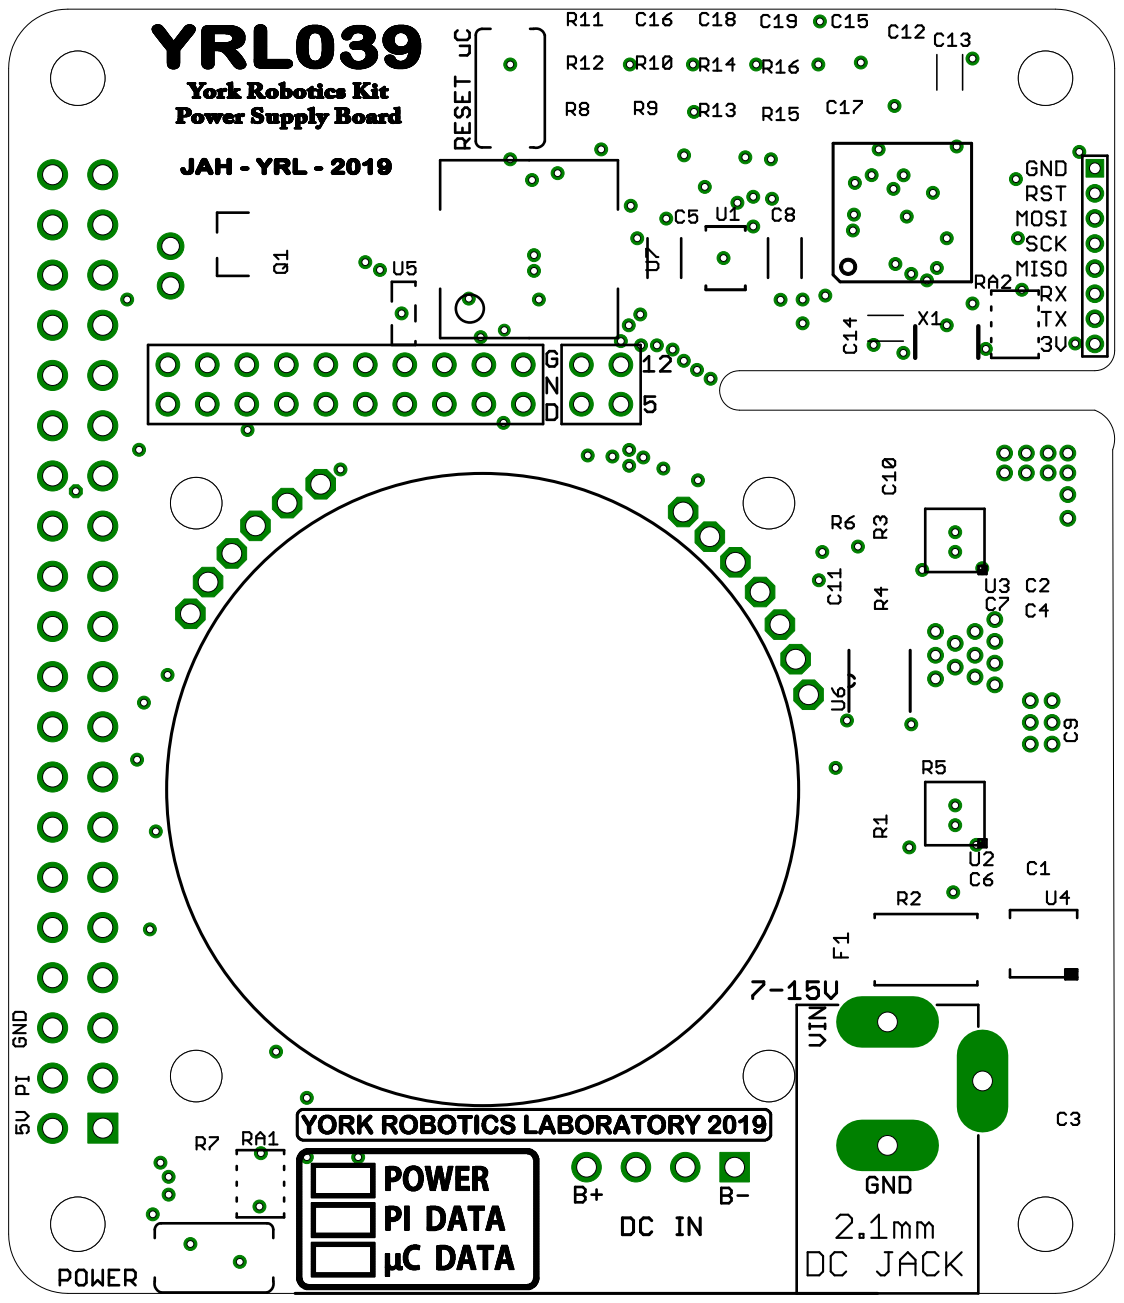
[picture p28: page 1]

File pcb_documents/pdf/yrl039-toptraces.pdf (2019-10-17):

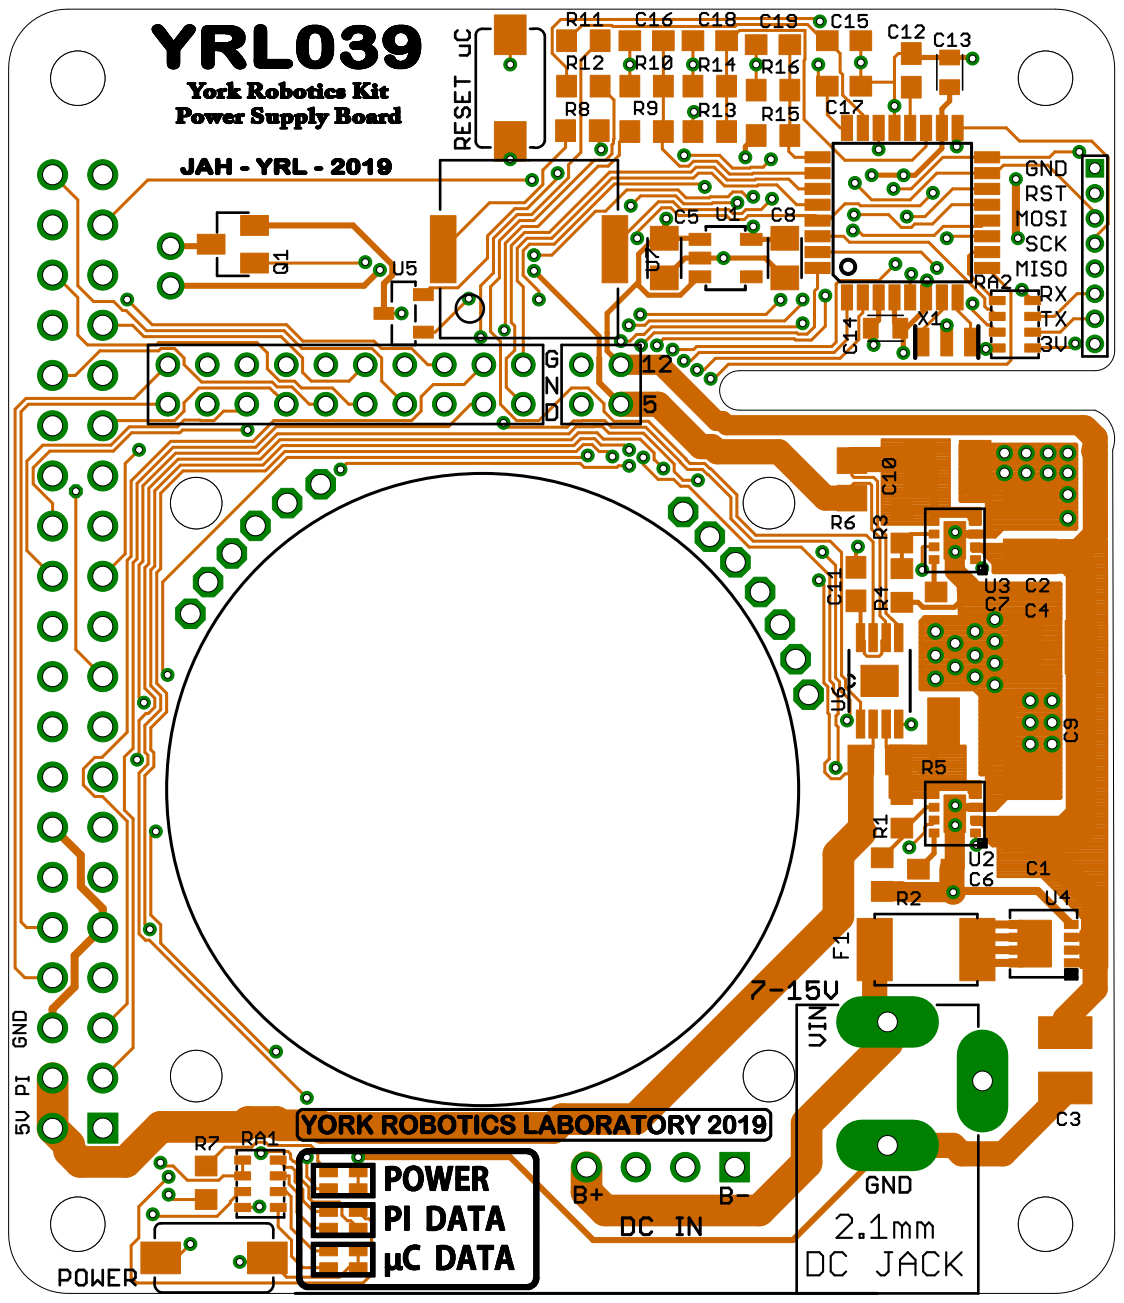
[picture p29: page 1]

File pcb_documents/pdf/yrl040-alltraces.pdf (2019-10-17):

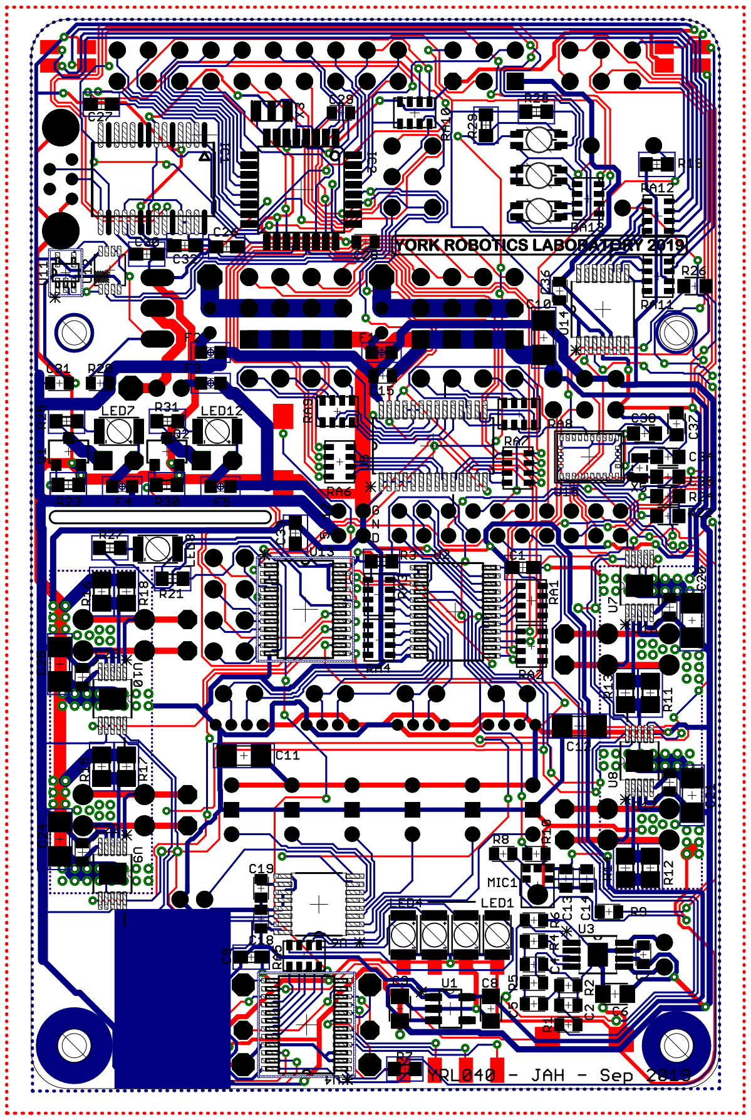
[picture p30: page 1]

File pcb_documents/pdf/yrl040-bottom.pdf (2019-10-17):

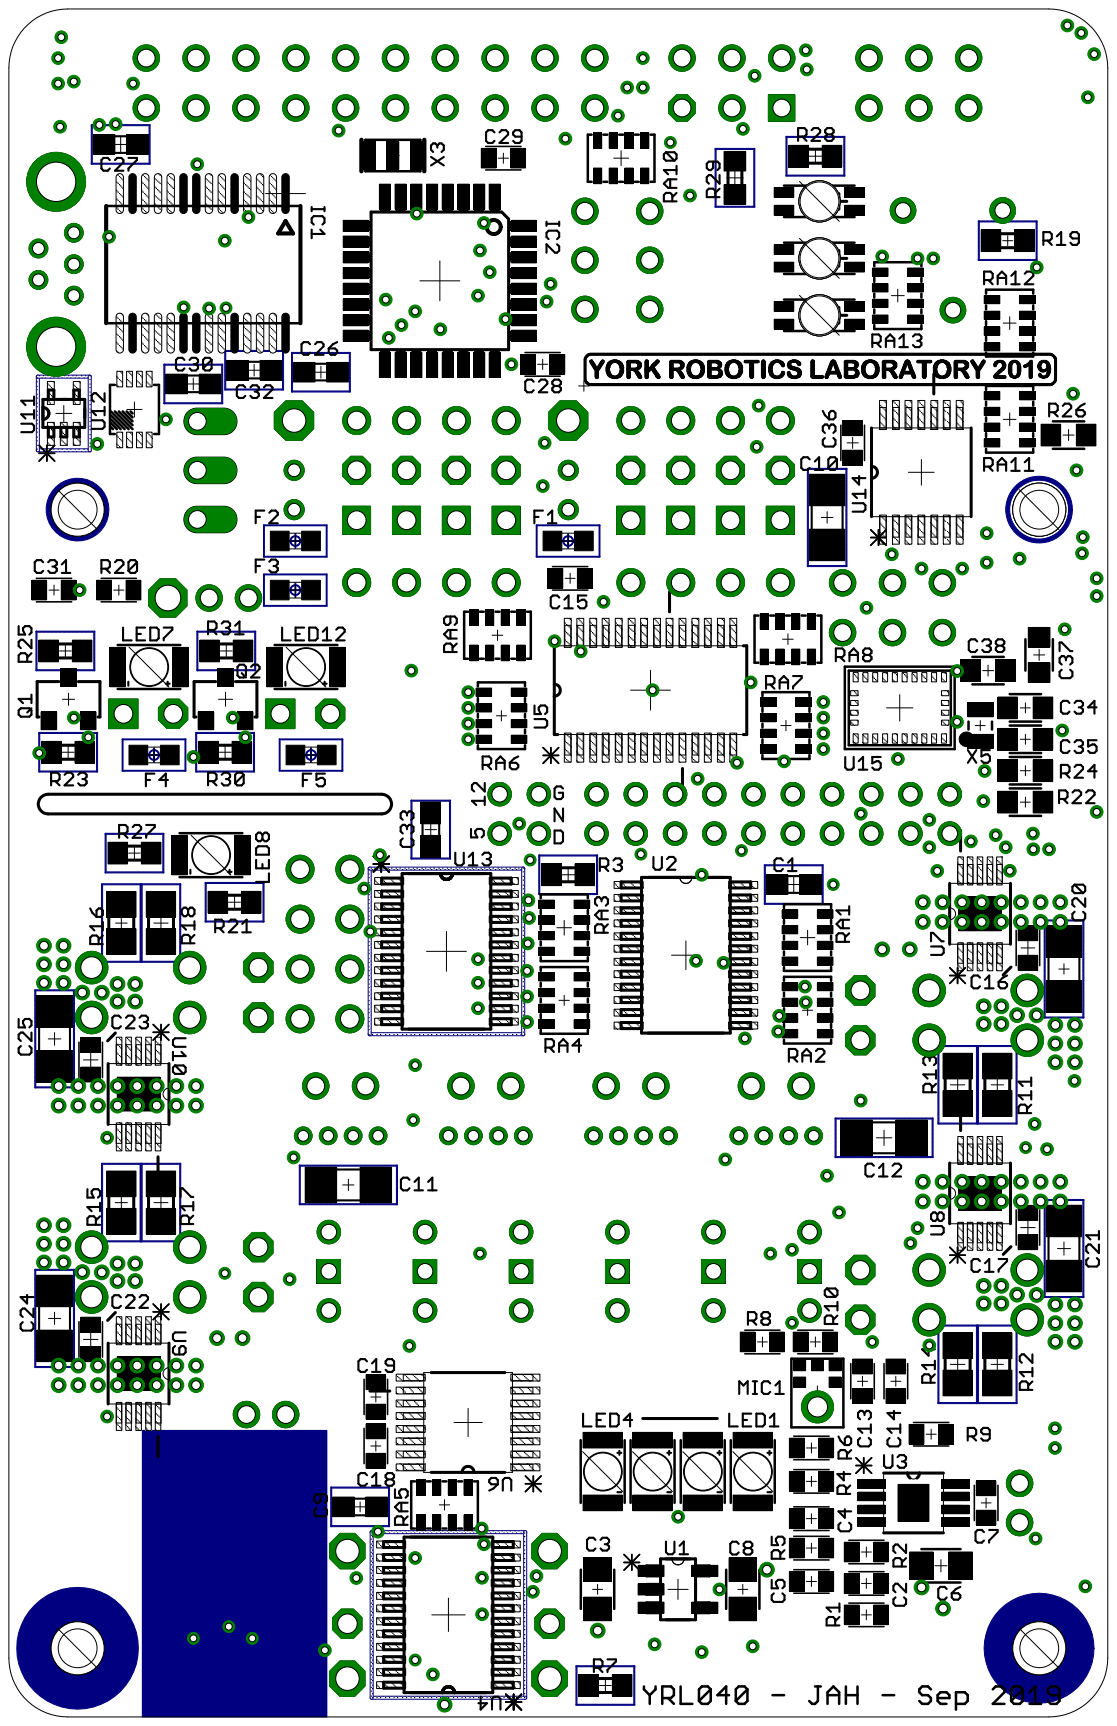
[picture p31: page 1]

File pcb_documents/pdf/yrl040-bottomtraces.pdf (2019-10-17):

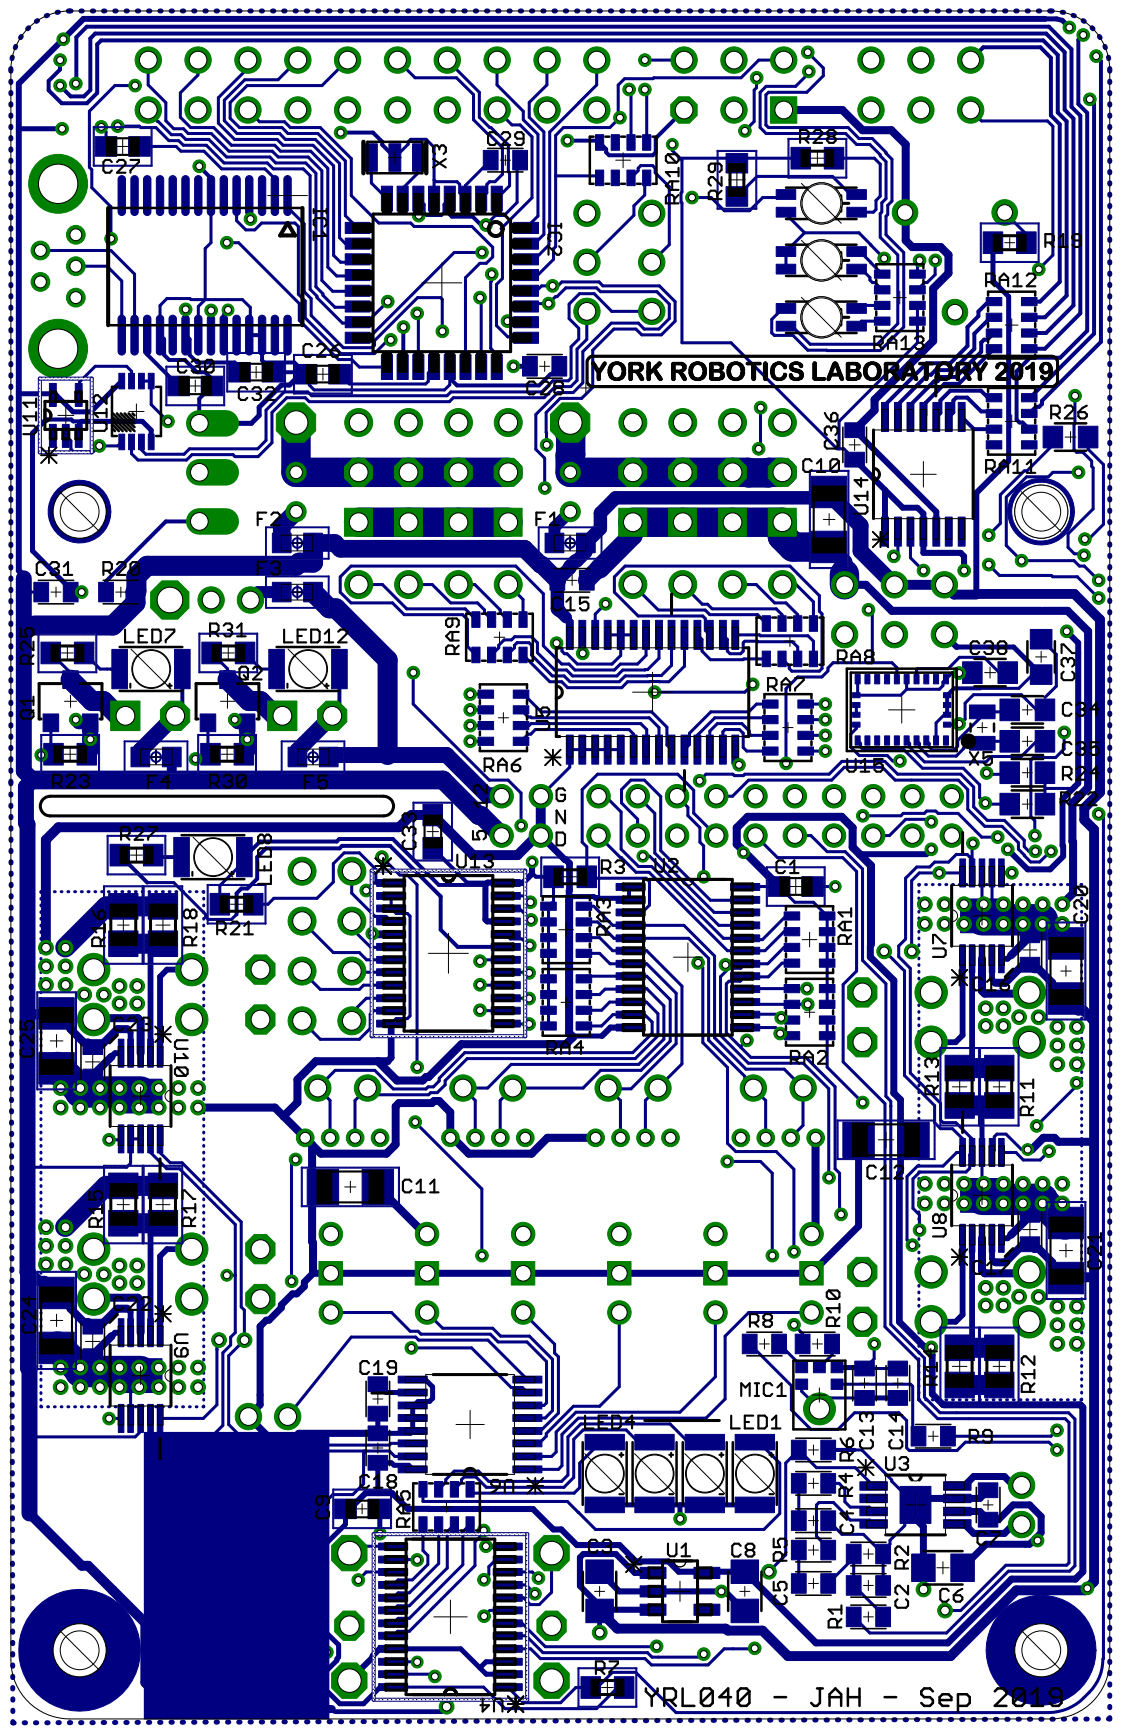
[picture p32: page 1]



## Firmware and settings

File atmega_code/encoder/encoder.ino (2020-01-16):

/*
 * Wheel Encoder example Arduino Code for the York Robotics Kit
 *
 * Copyright (C) 2020 James Hilder, York Robotics Laboratory,
 * University of York
 *
 * MIT License
 *
 * The York Robotics Kit main PCB [YRL040] includes an ATMega328P
 * microcontroller.  Its is effectively the equivalent of an
 * Arduino Nano, although with a different pin configuration.
 * It is intended to provide additional functionality, such as
 * counting wheel encoders and allowing the use of digital servo
 * motors.
 *
 * The microcontroller is connected to the I2C switch on the YRK,
 * on channel 4 [maps to /dev/i2c_10 on Pi 4].  The bus and
 * microcontroller operate at 5V.  The microcontroller has a 16 MHz
 * clock speed.
 *
 * This code is a simple example of its use for 2-motor wheel encoding.
 * It is designed for 5V tolerant wheel encoders such as the Pololu
 * magnetic and optical encoders for micro-metal gear motors.  If
 * using optical encoders ensure they are optimised for 5V operation.
 *
 * The Arduino has (only) two interrupt inputs [pins D2 and D3]. This
 * code assumes the (A) outputs of the encoders are connected to D2 and
 * D3, with the corresponding (B) outputs connected to A2 and A3.
 *
 * Power for the encoders can be taken from one of the PWM banks [ensure
 * that the jumper which connects the internal supply is attached].
 *
 */

#include <Wire.h>

const int i2c_slave_address = 0x57;
const int red_led = 12;
const int green_led = 13;

const int activity_led = A6;
const int motor_1_int = 2;
const int motor_1_dir = 3; 
const int motor_2_int = A2;
const int motor_2_dir = A3;
unsigned long startMillis;
volatile long enc_1_count = 0;
volatile long enc_2_count = 0;
volatile long enc_1_cumulative = 0;
volatile long enc_2_cumulative = 0;


void i2c_receive_event(int howMany) {
  Serial.println(howMany);
  while (1 < Wire.available()) { // loop through all but the last
    char c = Wire.read(); // receive byte as a character
    Serial.print(c);
  }
  Serial.println(" - i2c data");
}

void i2c_request_event() {
  Serial.println("Request event");
}

void enc_1_ISR() {
  boolean a = digitalRead(motor_1_int);
  boolean b = digitalRead(motor_1_dir);
  if(a==b) enc_1_count--;
  else enc_1_count++;
  enc_1_cumulative++;
}

void enc_2_ISR() {
  boolean a = digitalRead(motor_2_int);
  boolean b = digitalRead(motor_2_dir);
  if(a==b) enc_2_count++;
  else enc_2_count--;
  enc_2_cumulative++;
}

void reset_encoders() {
  enc_1_count=0;
  enc_2_count=0;
  enc_1_cumulative=0;
  enc_2_cumulative=0;
}


void setup() {
  // Setup serial console
  Serial.begin(57600);
  Serial.println(F("YRK-Arduino Wheel Encoder Code"));

  // Setup LEDs
  pinMode(red_led, OUTPUT);
  pinMode(green_led, OUTPUT);

  // Setup encoder pins and interrupts
  pinMode(motor_1_int, INPUT);
  pinMode(motor_1_dir, INPUT);
  pinMode(motor_2_int, INPUT);
  pinMode(motor_2_dir, INPUT);
  attachInterrupt(digitalPinToInterrupt(motor_1_int),enc_1_ISR,CHANGE);
  attachInterrupt(digitalPinToInterrupt(motor_2_int),enc_2_ISR,CHANGE);

  // Setup i2c connection
  Wire.begin(i2c_slave_address);
  Wire.onRequest(i2c_request_event);
  Wire.onReceive(i2c_receive_event);
  startMillis = millis();
}

void loop() {
  unsigned long currentMillis = millis() - startMillis;
  if(currentMillis > 1000) startMillis = millis();
  //Heartbeat blink with red led, 100ms every second
  if(currentMillis < 100) {if (!digitalRead(red_led)) digitalWrite(red_led,1);}
  else {if (digitalRead(red_led)) digitalWrite(red_led,0);}
}

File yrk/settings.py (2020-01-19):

#!/usr/bin/python
# York Robotics Kit Python API
#
# Version 0.21
#
# Settings and Constants File
#
# James Hilder, York Robotics Laboratory, Jan 2020



# Settings with docstrings are ones a user is likely to want\need to change

import logging,sys

VERSION_STRING="0.21.200120"

FILE_LOGGING_MODE = logging.DEBUG
"""Set the Python logging level for saved log files.

The recommend setting is logging.INFO for deployment and logging.DEBUG for debugging

"""

CONSOLE_LOGGING_MODE = logging.INFO  #Cannot be a lower level than FILE_LOGGING_MODE
"""Set the Python logging level for console output.

The recommend setting is logging.INFO for deployment and logging.DEBUG for debugging.
Cannot be at a lower level than FILE_LOGGING_MODE.

"""


#BUS Settings
#Note about busses:  RPi4 models have extra i2c busses so numbering for switch starts at I2C_7 [I2C_3 on Pi3 and earlier]

RASPBERRY_PI_MODEL = 4
"""Sets the Raspberry Pi version being used

   Set to 4 if using Raspberry Pi 4 (recommended)
   If set to different value, default BUS values are overwritten with values compatible with the earlier Pis.


"""

I2C_5V_BUS = 11
'''The PWM driver and the Arduino are on the 5V I2C Bus [bus 4 on switch]'''

OLED_BUS = 12
'''The /dev/i2c_XX bus which the OLED module is attached to'''

YRL040_BUS = 13
'''The /dev/i2c_XX bus the YRL040 [3.3V] I2C devoices are attached to'''

YRL039_BUS = 14
'''The /dev/i2c_XX bus the YRL039 Power Supply board's ATMega is attached to'''

#Use Raspberry Pi 3 bus settings
if (RASPBERRY_PI_MODEL != 4):
  I2C_5V_BUS = 7
  OLED_BUS = 8
  YRL040_BUS = 9
  YRL039_BUS = 10

#Display settings

HAS_DISPLAY = True
'''Set to True is OLED module is being used'''

DISPLAY_ROTATED = False
'''Set to True if the OLED module is rotated to flip image'''

#Audio Settings
AUDIO_VOLUME = 100
'''Volume to set Alsa mixer to on setup of audio (range 0-100, but 80+ recommended)'''

#PWM settings
PWM_FREQUENCY = 50
'''PWM (Analog Servo) target frequency in hertz'''

#ADC setting
ADC_MODELS = ['voltage','voltage','voltage','voltage','voltage','voltage','inv_pct','voltage']
"""List of model types for the 8 ADC inputs

   Sensor type in this list.  Should have 8 entries.  Note 7th is for potentiometer.
   Valid models are voltage, pct, inv_pct, raw, 2y0a21 and 2Y0a41

   Eg: ADC_MODELS              = ['2y0a21','2y0a41','voltage','raw','raw','raw','inv_pct','raw']


"""

ADC_NAMES = ['ADC 0','ADC 1','ADC 2','ADC 3','ADC 4','ADC 5','POT','ADC 7']

#GPIO settings
USER_GPIO_MODE = 0xFF
'''Initialisation mode for the 8 user GPIO pins [1=Input [with pull-up], 0=Output].'''

USER_GPIO_INVERTED = 0x00
'''Initialisation inversion state for the 8 user GPIO pins [1=Invert input]'''

USER_GPIO_OUTPUT_STATE = 0x00
'''Initialisation output state for the 8 user GPIO pins'''

#YRK-core settings
BATTERY_CHECK_PERIOD = 2.0
'''Period (s) between battery state checks'''

TEMPERATURE_CHECK_PERIOD = 2.0
'''Period (s) between temperature checks'''

ENABLE_BATTERY_MONITOR = True
'''If enabled yrk-core.py will display visual+audible warnings when battery low'''


ENABLE_TEMPERATURE_MONITOR = True
'''If enabled yrk-core.py will display visual+audible warnings when cpu\pcb temperature high'''

BATTERY_CRITICAL_SHUTDOWN = True
'''If enabled, system will force shutdown when Vbatt<BATTERY_SHUTDOWN_VOLTAGE'''

TEMPERATURE_CRITICAL_SHUTDOWN = True
'''If enabled, system will force shutdown when CPU Temp<CPU_SHUTDOWN_TEMP or PCB Temp<PCB_SHUTDOWN_TEMP'''

BATTERY_CELLS = 2
"""Number of Li-Ion or Li-Po cells in battery (2,3 or 4)

   Sets the BATTERY_LOW_VOLTAGE, BATTERY_CRITICAL_VOLTAGE and BATTERY_SHUTDOWN_VOLTAGE parameters
   based on the number of cells described.  The values for 2 cell batteries are a little more generous
   to get decent usable life of of battery, although voltage drop may be too great in high current
   drain use cases.  If using other battery technology (eg Ni-Mh) set values manually within settings.py


 """

CPU_WARNING_TEMP = 65
'''CPU warning temperature, recommend ~65C for Pi 4 and ~60C for Pi 3'''

CPU_CRITICAL_TEMP = 75
'''CPU critical temperature, recommend ~75C for Pi 4 and ~65C for Pi 3'''

CPU_SHUTDOWN_TEMP = 82
'''CPU shutdown temperature, recommend ~82C for Pi 4 and ~72C for Pi 3'''

PCB_WARNING_TEMP = 40
'''PCB warning temperature, recommend ~40C'''

PCB_CRITICAL_TEMP = 45
'''PCB critical temperature, recommend ~45C'''

PCB_SHUTDOWN_TEMP = 50
'''PCB forced shutdown temperature, recommend ~50C'''

USE_DIP_FUNCTIONS = True
'''If True, yrk-core uses DIP 2 for ROS, DIP 3 for DASH server and DIP 4 for DEMO'''

USE_DIP_LEDS = True
'''If true, yrk-core will set DIP LEDs based on program state'''

YRL039_ADDRESS = 0x39
'''The I2C address for the ATMega on the YRL039 Power Supply Board (could be reprogrammed to different address if needed).'''
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

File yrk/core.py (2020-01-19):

#!/usr/bin/python
#
# York Robotics Kit Python API
# Version 0.21
# Core services
#
# In normal use, a single instance of this should be run as a program when
# using the York Robotics Kit.  This is done automatically on boot by the
# .bashrc and yrk/bootscript.sh scripts.
#
# James Hilder, York Robotics Laboratory, Jan 2020

"""
.. module:: core
   :synopsis: Core services module

.. moduleauthor:: James Hilder <github.com/jah128>

The core module provides the low level hypervisory functions for normal
use of the York Robotics Kit.  This includes the following list of operations,
which are periodically checked:

 * Low and critical battery level monitoring
 * High and critical temperature monitoring
 * Fault conditions and low-voltage on the aux- and pi- supply rails
 * Monitoring of DIP-switches and kill-switch, creating switch status file

The module is responsible for handling DIP-switch changes.  It is by default
run automatically by the bootscript.sh script if DIP switch 1 is enabled.
Assuming it is, the module then handles launching the ROS services if DIP switch
2 is enabled [and terminating them if is disabled], and likewise launching and
closing the DASH-DAQ web interface is DIP switch 3 is enabled and disabled.


"""

#Setup settings file and log
import yrk.settings as settings, logging, os
import dashserver.server as server

import threading,time, sys, subprocess, signal
import multiprocessing as mp
import psutil
import yrk.power as power
import yrk.switch as switch
import yrk.utils as utils
import yrk.led as led
import yrk.display as display
import yrk.audio as audio
import yrk.motors as motors
import yrk.gpio as gpio

#Setup GPIO library and interrupt pins
import RPi.GPIO as GPIO

#Globals
core_running = True
battery_check_requested = False
temperature_check_requested = False
switch_check_requested = True
gpio_check_requested = True
previous_switch_state = 0
previous_gpio_state = 0
battery_warning_state = 0
temperature_warning_state = 0
ros_running = False
demo_running = False
dash_server_process = None

def switch_interrupt_callback(pin):
  global switch_check_requested
  switch_check_requested = True

def gpio_interrupt_callback(pin):
  global gpio_check_requested
  gpio_check_requested = True

def main():
  #mp.set_start_method('spawn')
  settings.setup_logger("core")
  logging.info("York Robotics Kit Core Server [core.py] Started - Version %s" % (settings.VERSION_STRING))
  logging.info("YRK core PID: %d " % (os.getpid()))
  reset_all()
  #Setup GPIO pins, interrupts
  GPIO.setmode(GPIO.BCM)
  GPIO.setup(settings.SWITCH_INTERRUPT_PIN,GPIO.IN,pull_up_down=GPIO.PUD_UP)
  GPIO.add_event_detect(settings.SWITCH_INTERRUPT_PIN , GPIO.FALLING, switch_interrupt_callback)
  GPIO.setup(settings.GPIO_INTERRUPT_PIN,GPIO.IN,pull_up_down=GPIO.PUD_UP)
  GPIO.add_event_detect(settings.GPIO_INTERRUPT_PIN , GPIO.FALLING, gpio_interrupt_callback)
  #Setup debug LED
  GPIO.setup(settings.DEBUG_LED_PIN,GPIO.OUT)

  #Setup audio thread
  audio.setup_audio()
  #Start update timer threads
  start_threads()
  core_loop()
  logging.info("Core loop terminated")

def shutdown():
    logging.critical("Battery voltage critically low, shutting down.")
    time.sleep(0.5)
    os.system("shutdown")

def start_ros():
    if not is_ros_running():
        logging.info("Starting ROS services")
        subprocess.Popen(settings.ROS_LAUNCH_COMMAND)
    else:
        logging.warning("ROS appears to be already running (PID file exists)")

def stop_ros():
    if is_ros_running():
        #subprocess.Popen(settings.ROS_KILL_COMMAND)
        with open(settings.ROS_PID_FILE) as file:
            ros_pid = int(file.read())
            logging.info("Stopping ROS services [killing ROSLAUNCH PID %d]" % ros_pid)
            os.kill(ros_pid, signal.SIGINT) #or signal.SIGKILL
    else:
        logging.warning("ROS does not appear to be running (no PID file)")

def start_dash():
    global dash_server_process
    if not is_dash_running():
        logging.info("Starting DASH web server")
        #dash_pid = subprocess.Popen(settings.DASH_LAUNCH_COMMAND).pid
        #logging.info("PID: %d" % dash_pid)
        #subprocess.Popen(["python",""])
        dash_server_process = mp.Process(target=server.index_run)
        #dash_server_process.daemon=True
        dash_server_process.start()
        logging.info("dash server PID: %d " % (dash_server_process.pid))
        #dash_server_process.join()
    else:
        logging.warning("DASH appears to be already running (PID file exists)")

def stop_dash():
    global dash_server_process
    if is_dash_running():
        logging.info("Terminating DASH server")
        parent = psutil.Process(dash_server_process.pid)
        for child in parent.children(recursive=True):
            try:
                child.kill()
            except psutil.NoSuchProcess:
                pass
        dash_server_process.terminate()
    else:
        logging.warning("DASH is not currently running")


def dip_switch_handler(current_dip_state,previous_dip_state):
  #The DIP switch has changed state...
  logging.debug('DIP Switch state altered')
  if current_dip_state & 1 == 1 and previous_dip_state & 1 == 0:
    logging.debug("DIP 1 enabled")
  if current_dip_state & 1 == 0 and previous_dip_state & 1 == 1:
    demo_mode_enabled = False
    logging.debug("DIP 1 disabled")
  if current_dip_state & 2 == 2 and previous_dip_state & 2 == 0:
    logging.debug("DIP 2 enabled (starting ROS services)")
    start_ros()
  if current_dip_state & 2 == 0 and previous_dip_state & 2 == 2:
    logging.debug("DIP 2 disabled (stopping ROS services)")
    stop_ros()
  if current_dip_state & 4 == 4 and previous_dip_state & 4 == 0:
    logging.debug("DIP 3 enabled (starting DASH-DAQ server)")
    start_dash()
  if current_dip_state & 4 == 0 and previous_dip_state & 4 == 4:
    logging.debug("DIP 3 disabled (stopping DASH-DAQ server)")
    stop_dash()
  if current_dip_state & 8 == 8 and previous_dip_state & 8 == 0:
    logging.debug("DIP 4 enabled: Starting demo mode")
  if current_dip_state & 8 == 0 and previous_dip_state & 8 == 8:
    logging.debug("DIP 4 disabled: Stopping demo mode")

def is_ros_running():
    return os.path.isfile("/mnt/ramdisk/roslaunch.pid")

def is_dash_running():
    if dash_server_process is None: return False
    return dash_server_process.is_alive()

def update_dip_leds():
    #Running this function periodically will check if ROS and C
    while core_running:
        byte = 0
        if core_running: byte += 1;
        if is_ros_running(): byte += 2;
        if is_dash_running(): byte += 4;
        if demo_running: byte += 8;
        switch.set_dip_leds(byte)
        time.sleep(1)
    switch.set_dip_leds(0)
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

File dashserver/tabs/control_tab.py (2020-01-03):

# YRL028 - APIHAT - Dash-DAQ Server Version 0.1
#
# Control Tab
#
# James Hilder, York Robotics Laboratory, Feb 2019

import dash
import dash_core_components as dcc
import dash_html_components as html
import dash_daq as daq
from dash.dependencies import Input, Output, State
import yrk.led as led, yrk.audio as audio, yrk.display as display, yrk.motors as motors, yrk.settings as settings, yrk.utils as utils, os

from app import app

audio.start_audio_thread()
import css
flex_style =css.flex_style
border_style = css.border_style
block_style = css.block_style

def create_div(title,body):
    return html.Div([html.H6(title),html.Div(body,style=flex_style)],style=border_style)

layout = html.Div([
    create_div('Audio',[
        html.Div([
            html.Div([
                html.H6("Volume"),
                daq.Slider(id="volume-slider",value=settings.AUDIO_VOLUME,min=0,max=100,updatemode="drag",handleLabel={"showCurrentValue":True,"label":"SPEED"}),
            ]),
            dcc.Dropdown(
                id='audio-file-dropdown',
                options=[{'label':i,'value':str(count)} for count,i in enumerate(utils.get_audio_filelist())]
            ),
            html.Div(id='playback-div'),
            html.Div(id='volume-callback-div'),
        ]),
    ]),
    create_div('Text to Speech',[
        dcc.Input(placeholder='Text to say...',type='text',value='',id=('speech-text-field')),
        html.Button('Speak', id='speak-button'),
        html.Div(id='speech-callback-div')
    ]),
    create_div('Speech to Text',[
        html.Button('Start Recording', id='record-button'),
        html.Div(id='speech-to-text-callback-div')
    ]),
    create_div('I2C Motors',[
        html.Div([
            html.H6("Motor 1"),
            daq.Slider(id="motor1-slider",value=0,min=-100,max=100,updatemode="drag",handleLabel={"showCurrentValue":True,"label":"SPEED"}),
        ]),
        html.Div([
            html.H6("Motor 2"),
            daq.Slider(id="motor2-slider",value=0,min=-100,max=100,updatemode="drag",handleLabel={"showCurrentValue":True,"label":"SPEED"}),
        ]),
        html.Button('Stop', id='stop-button'),
        html.Div(id='motor-output-div'),
    ]),
    create_div('Body LED',[
        html.Div([
            html.H6("Solid Colour"),
            dcc.Dropdown(id='control-app-bodyled-dropdown',options=[{'label':i[0],'value':str(count)} for count,i in enumerate(led.solid_colours)])
        ],style=block_style),
        html.Div(id='control-app-bodyled'),
        html.Div([
            html.H6("Animation"),
            dcc.Dropdown(id='animation-dropdown',options=[{'label':i[0],'value':str(count)} for count,i in enumerate(led.body_animations)]),
        ],style=block_style),
        html.Div(id='animation-div'),
        ]),
    create_div('OLED Display',[
        dcc.Input(placeholder='Text to display...',type='text',value='',id=('display-text-field')),
        html.Button('Display', id='display-button'),
        html.Div(id='display-callback-div')
    ]),
])

#Audio callbacks
@app.callback(
    Output('volume-callback-div', 'children'),
    [Input('volume-slider', 'value')])
def volume_callback(v):
    audio.set_volume(v)
    return(html.P("Setting volume to %d" % (v)))

@app.callback(
    Output('playback-div', 'children'),
    [Input('audio-file-dropdown', 'value')])
def audio_callback(value):
    if(value==None): return('')
    audio.play_audio_file(os.path.join(settings.AUDIO_FILEPATH,utils.get_audio_filelist()[int(value)]))
    return html.P("Playing audio file %s" % (utils.get_audio_filelist()[int(value)]))


#Motor control callbacks
@app.callback(
    Output('motor1-slider','value'),
    [Input('stop-button','n_clicks')])
def stop_motor1_callback(c):
    return 0

@app.callback(
    Output('motor2-slider','value'),
    [Input('stop-button','n_clicks')])
def stop_motor2_callback(c):
    return 0

@app.callback(
    Output('motor-output-div', 'children'),
    [Input('motor1-slider', 'value'), Input('motor2-slider','value')])
def motor_speed_callback(m1,m2):
    motors.set_motor_speeds(m1/100.0,m2/100.0)
    return(html.P("Setting motor 1 to %d, motor 2 to %d" % (m1,m2)))

#Speech to text callback
@app.callback(
    Output('speech-to-text-callback-div', 'children'),
    [Input('record-button', 'n_clicks')])
def speech_to_text_callback(c):
    if c == None: return ''
    if c % 2 == 1:
        #Odd number: start Recording
        led.animation(2)
        speech.start_recording()
        return (html.P("Recording audio - press again to stop"))
    response = speech.end_recording()
    led.animation(0)
    return (html.P("Google Response: %s" % response))

@app.callback(
    Output('speech-callback-div', 'children'),
    [Input('speak-button', 'n_clicks')],
    [State('speech-text-field','value')])
def speech_callback(c,value):
    if c == None: return ''
    audio.unmute()
    audio.IF_say(value)
    return (html.P("%s spoken." % value))

@app.callback(
    Output('display-callback-div', 'children'),
    [Input('display-button', 'n_clicks')],
    [State('display-text-field','value')])
def speech_callback(c,value):
    if c == None: return ''
    display.one_line_text_wrapped(value)
    return (html.P("%s sent to OLED display." % value))


@app.callback(
    Output('animation-div', 'children'),
    [Input('animation-dropdown', 'value')])
def animation_callback(value):
    if value == None: return ''
    led.animation(int(value))
    return ''

@app.callback(
    Output('control-app-bodyled', 'children'),
    [Input('control-app-bodyled-dropdown', 'value')])
def control_app_bodyled_callback(value):
    if value== None: return ''
    led.set_colour_solid(int(value))
    return ''

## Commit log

2019-10-11 Added first version of pwm module
2019-10-17 Added YRL039 Arduino code
2019-10-17 Added design PDFs, Eagle files, BOM documents
    [yrl039-bom.xlsx, yrl039-final.brd, yrl040-bill-of-materials.xlsx]
2019-10-20 Added servo functionality to console, added new servo functions
2019-10-21 Changed console to use wrapper() to fix exit errors
    [console.py]
2019-11-02 Added error checking for case when i2c bus doesn't exist
    [adc.py, display.py, gpio.py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]
2019-11-26 Added button rublisher
2019-11-27 Added LED ROS service, launch files
2020-01-02 Fixed paths and added warning image
    [display.py, settings.py, yrk-core.py]
2020-01-03 Added copy of dash server from yrl028; not in working order. Added roslaunch and dash launch functionality; problem with multiprocessing library using dash as it threads [duplicates main program]. To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
    [analog_tab.py, camera_tab.py, control_tab.py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]
2020-01-03 Bugfix in audio; added override to pwm selftest
    [audio.py, selftest.py, settings.py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]
2020-01-03 Version code 0.2; added i2c lock mutex functions in utils and use by all relevant modules
2020-01-06 Added motor ros service
2020-01-06 Added display ros service, 2-cell option to battery voltages
2020-01-10 Added PCB images to user guide
2020-01-14 Renamed yrk-core to core [hyphen breaks sphinx], split into multiple .rst [need to fix toctree].
    [core.py]
2020-01-14 Fixed TOC issue in docs
    [console.py]
2020-01-15 Added encoder code folder and upload script [to fix]
    [encoder.ino]
2020-01-16 Updated user guide; bugfix encoder.ino
    [encoder.ino]
2020-01-17 Added error checking for font files
    [display.py]
2020-01-19 Added documents section to user guide, fixed some readthedocs import problems, added pbm images
    [yrl039-1_0.brd, yrl039-final.brd]
2020-01-19 Added gpio (motor fault monitoring etc) to core
2020-01-20 Added i2c section to user guide
